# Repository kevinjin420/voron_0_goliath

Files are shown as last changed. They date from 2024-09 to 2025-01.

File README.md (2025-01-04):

# Vector Toolhead

The vector toolhead is an ultra high-performance toolhead designed for the Voron 0.2 as well as various [Printers for Ants](https://3dprintersforants.com/).

It has been specifically designed for the Goliath Air V2 toolhead menufactured by Mellow (available on [Aliexpress](https://www.aliexpress.us/item/3256805112047958.html) and other retailers) as well as the Orbiter V2.0 from LDO Motors. Such a configuration allows for maximum flowrate up to 110mm<sup>3</sup>/s. 

It uses a CNC-machined X-carriage backplate (available [here](https://www.aliexpress.us/item/3256803869616066.html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)), which helps with the overall rigidity of the toolhead. Note that a skeleton X-beam is **not** recommended for ultra high-speed printing, as the reduction in torsional stiffness leads to a noticeable decrease in print quality. 

The toolhead is designed to be used with auxiliary fans, meaning that there are no part cooling fans onboard, but instead rely on a stationary-mounted auxiliary fan system such as the [V0 Auxiliary Fan](https://github.com/JackJack3231/V0-Auxiliary-Fan) mod by JackJack3231. Such a configuration reduces wiring complexity as well as moving mass, which allows for higher accelerations. 

**Unfortunately, this also means that the Vector toolhead is incompatible for printers that use a flying gantry, such as the [F-Zero](https://github.com/zruncho3d/f-zero) and the [Micron](https://github.com/PrintersForAnts/Micron). (unless you can get the aux fan to move with a flying gantry)** 

Optionally, for improved torque and motor support, the [Voron V0.2 Nema 17 Mount](https://www.printables.com/model/494742-voron-v02-nema-17-mount) by redirector allows for the installation of larger Nema 17 motors that is able to handle higher current and output more torque. 

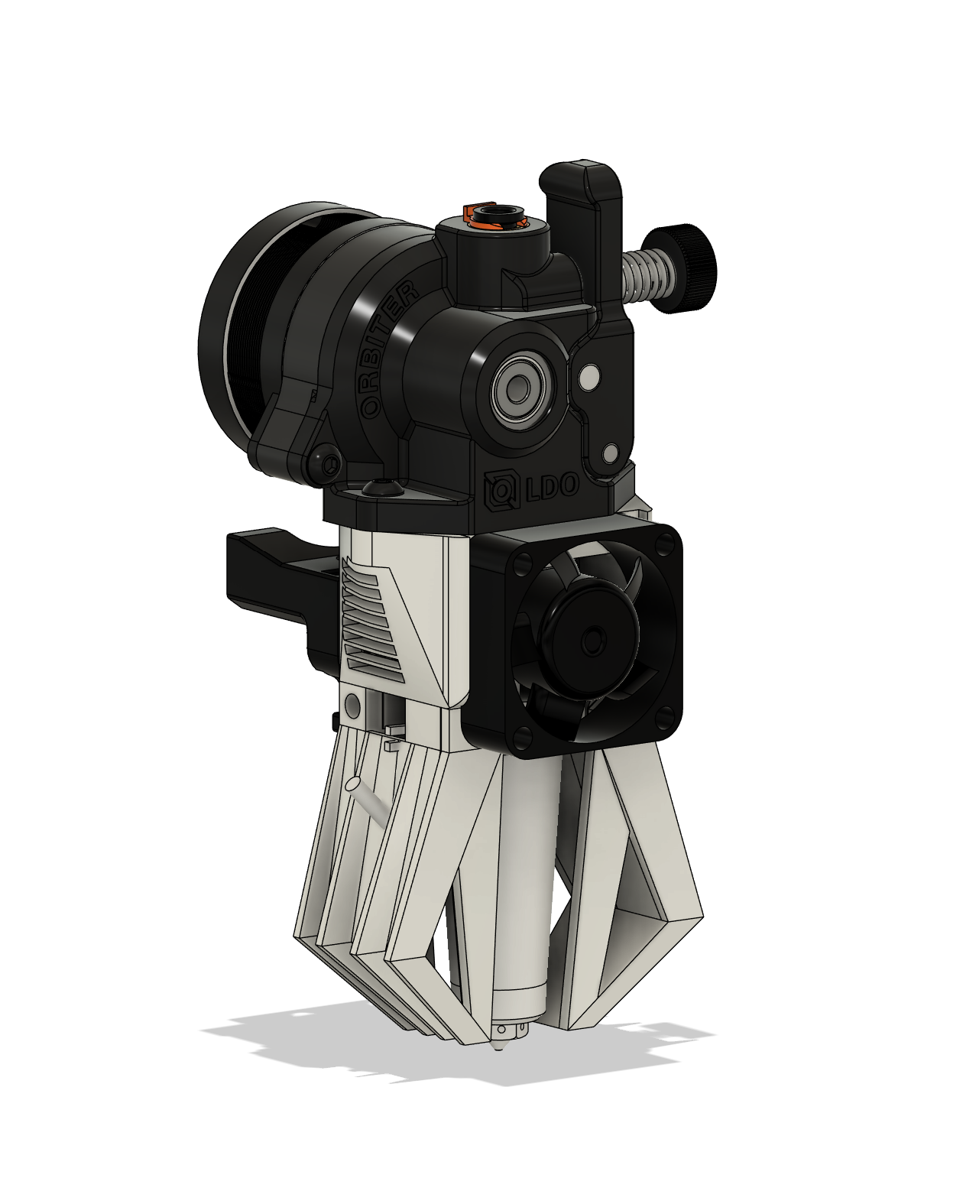
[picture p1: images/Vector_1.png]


# BOM

| Component | Quantity | Link |
| --- | --- | --- |
| Goliath Air V2 | 1 | [Aliexpress](https://www.aliexpress.us/item/3256805112047958.html)|
| X-gantry Backplate | 1 | [Aliexpress](https://www.aliexpress.us/item/3256803869616066.html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)
| M3 Heatset Inserts | 7 | [Amazon](https://www.amazon.com/dp/B0CDH36ZMX?ref_=ppx_hzsearch_conn_dt_b_fed_asin_title_1)
| M3 Nuts and Bolts | 1 | [Amazon](https://www.amazon.com/dp/B07L65DHV6?ref_=ppx_hzsearch_conn_dt_b_fed_asin_title_2) |
| 3007 24V Fan | 1 | [Aliexpress](https://www.aliexpress.us/item/3256804799089065.html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)

# Installation and Assembly

Needless to say, this hotend assembly should be printed using ABS, which has a deformation temperature high enough for the needs of a 3D printer hotend. 

First, apply the 7 Heatset Inserts to the positions indicated below. Secure the cowling to the X-gantry backplate before continuing. Then, use the four screws provided with your Goliath Air, and secure it to the main cowling, ensuring that the thermistor wires and heater coil cables run out through the rectangular section on the left of the cowling. 

Secure the side air ducts to the main cowling, then fit the 3007 fan over the front, ensuring that the screw holes line up. Be careful not to overtighten the two bottom screws so that you do not strip the plastic. The heater and thermistor cables should run above the left air duct piece, exiting upwards and joining your wiring harness. 

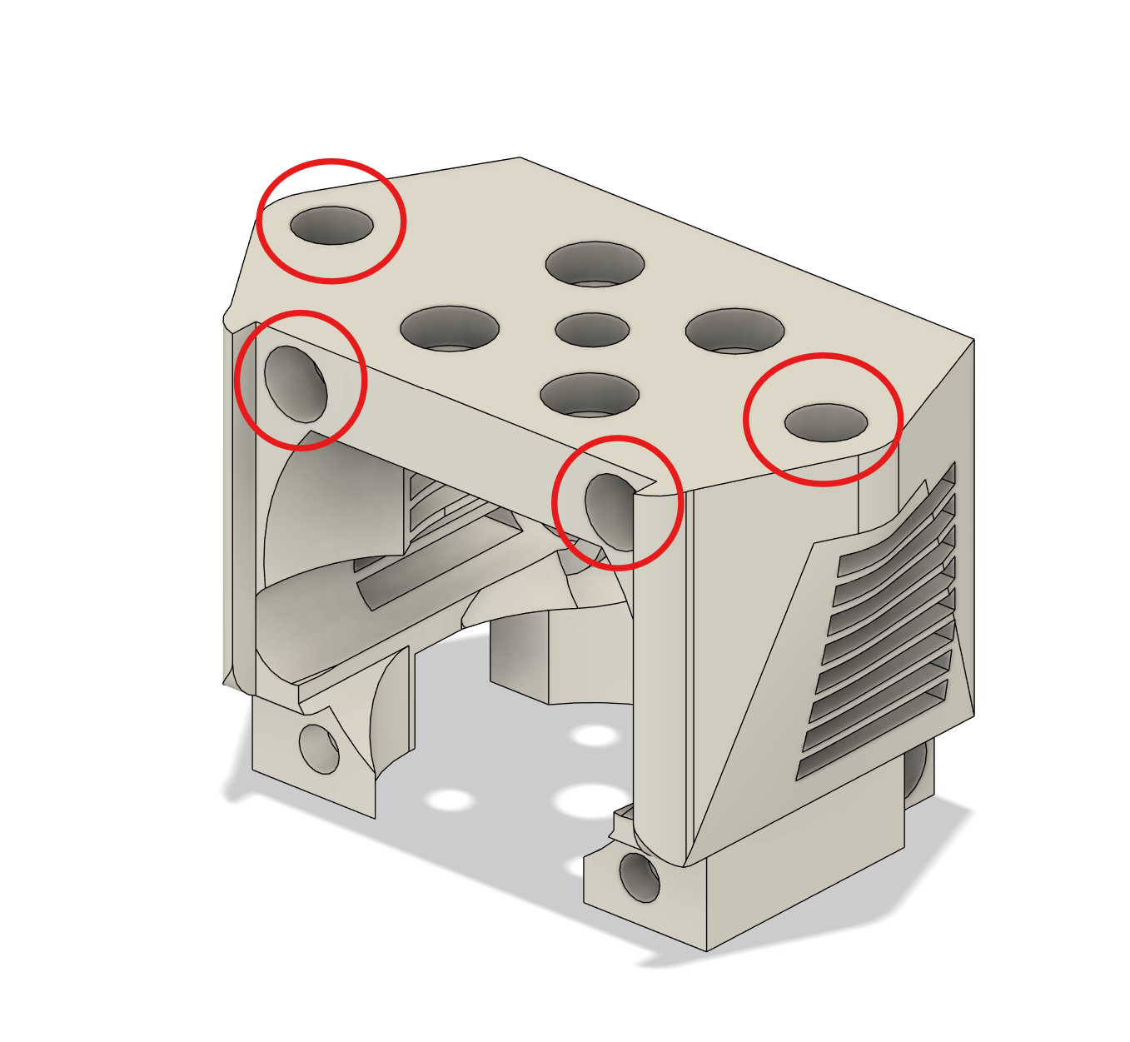
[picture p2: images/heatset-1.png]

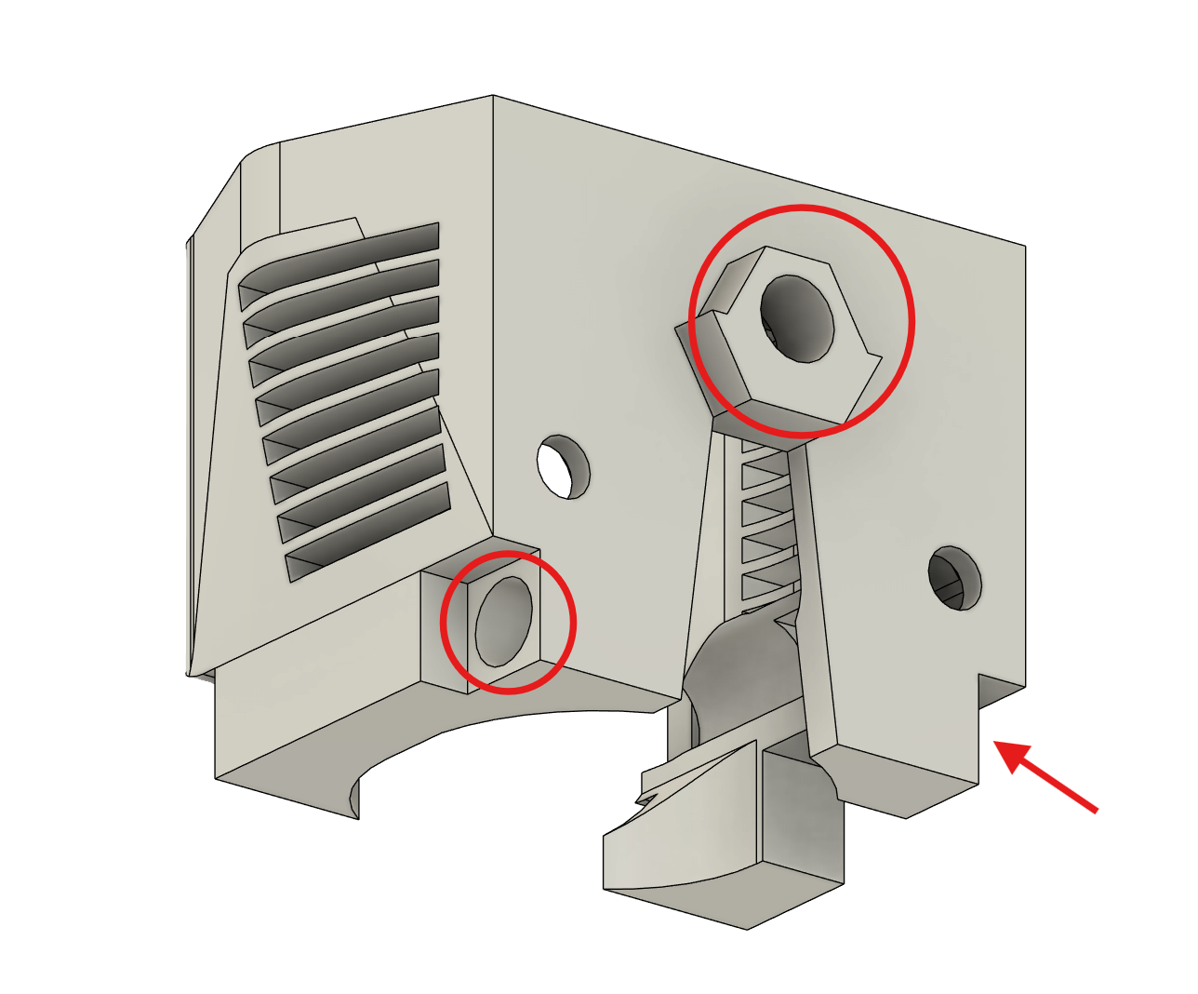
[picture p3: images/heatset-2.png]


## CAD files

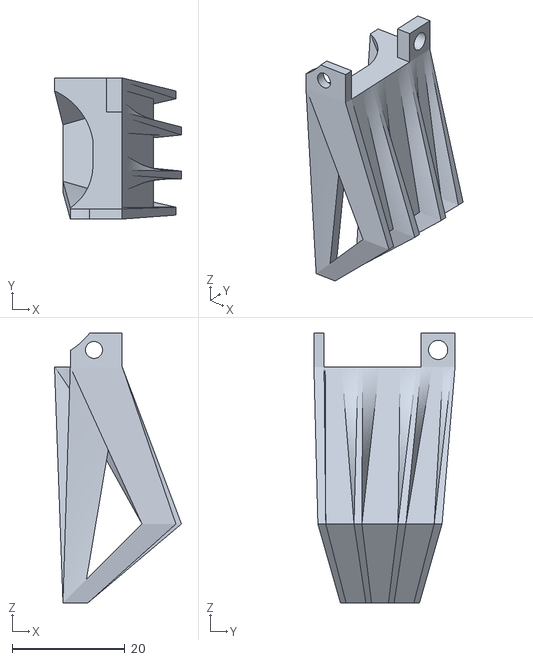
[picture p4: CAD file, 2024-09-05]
STLs/right_cowl.stl
22.5 x 25.0 x 47.8

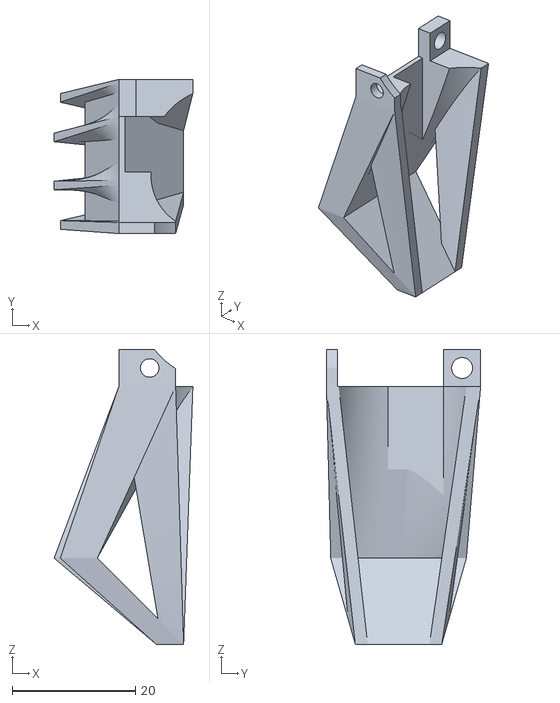
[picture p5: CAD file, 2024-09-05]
STLs/left_cowl.stl
22.5 x 25.0 x 47.8

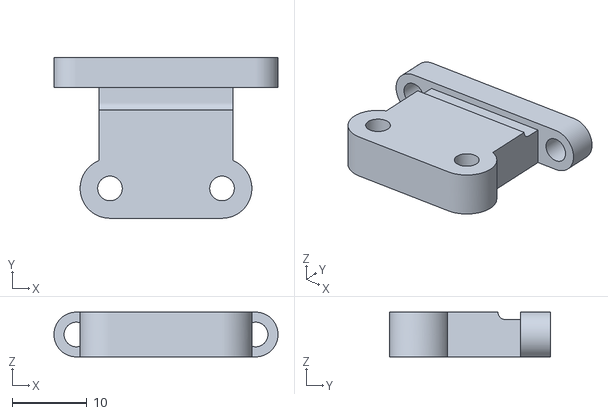
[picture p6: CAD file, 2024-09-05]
STLs/adxl_mount.stl
30.0 x 21.5 x 6.00

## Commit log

2024-09-05 added stls
    [adxl_mount.stl, left_cowl.stl, right_cowl.stl]
2024-09-05 added cad
